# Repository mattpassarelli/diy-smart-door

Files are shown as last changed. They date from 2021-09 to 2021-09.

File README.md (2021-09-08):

# DIY Smart Door
This is, ideally, going to be a relatively universal smart door/lock adapter made from an ESP8266/ESP32 and one-two MG995 servos. More on what each servo does in the next section. This would then be connected to my home WiFi network where I can integrate it into Home Assistant for any kind of automation I would want to add, like opening the door for my friends without the need of me getting up from the couch :). 

## Design

Using an ESP8266 specifically (as I save my ESP32's for other projects), it's going to have 2 servos wired to it to open my door. If you choose the copy this project, I would guarantee you that like >90% of people only need 1 servo. ~~My current apartment's door is this weird style I've never seen where you *have* to use the key to open the door, regardless of whether or not anything is locked. Meaning, I only really have a deadbolt, and not a latch lock that I can engage and disengage. So even if I left the deadbolt unlocked all the time, you would need a key to be able to turn my door's latch and handle to enter my apartment.~~ I have what's called a Store Room style latch. I'm going to work off the assumption that my apartment will switch it out for me (going off the reasons that I risk getting locked out frequently, which technically isn't wrong); so we'll only need the one main servo for now*.

So, now the mechanical design ideas; There are a few 3D models in this repo that should be fairly universal. Right now, both planned and ready are:
- the housing for the servo that will be secured to the door over the deadbolt
- the latch cover that goes over my deadbolt and fits one of the servo horns
- a housing for the arduino and a battery and charger
- and the servo housing for the door handle portion*

That list might be updated as I add or remove parts from my design.

There are also 2-3 buttons for this system: 

- a lock button
- an unlock button
- an unlock iff locked, then turn handle button*

### Servo One
The first servo will be secured in housing that is then, most likely, command stripped to the door. 1) because I don't want to damage the door by screwing into it, and 2) if something were to happen where I need to immediately exit my home, I could rip the whole thing off in one swoop and then repaint easily if anything got damaged. 

This servo is connected to the deadbolt by an adapter that sits on top of the bolt and has a horn glued into it. The first motion of the whole overarching code will be to turn this servo 150° clockwise to unlock, then the same degrees counter clockwise to close (the number will change based on your deadbolt, so be sure to measure). This will have a timer running, so that if the lock is unlocked for, say 10 minutes, it will automatically lock it, giving me some peace of mind. I do also plan on integrating some automation logic into this with Home Assistant that might mitigate the need for this, but either will do the trick. 

Right now, this is controlled by a button on my breadboard, but I have plans to automate this with Home Assistant later.

### Servo Two, the door "opener"*
This is the one that not everyone will need, but you may need something like Servo One attached to your latch lock if you have a "normal" door. This one will be to the side of the deadbolt, positioned directly above the very edge of the door handle. With a stiff rod attached to a horn, maybe like a hanger wire or wooden dowel, and the other end on a free moving pivot on the door handle, this servo will turn *after* the deadbolt is unlocked and if **and only if** the deadbolt is fully unlocked. This is will the last part of my "hardware portion" of this project, so this might vary greatly by the time I've figured out how best to do this.

This one will be a third button that unlocks the deadbolt if it isn't already unlocked, then turn the servo, "opening" the door for someone to be able to push open the door. Then it will release the handle after a very short amount of time, say 5 seconds, so that the door can close on it's own and lock itself like normal (I have one of those hydraulic arms attached the top of the door that automatically closes it and was there when I signed my current apartment).

*Right now, I'm trying to get my door handle's replaced by the apartment (so they still have legal, master access when needed). So this second servo will ideally be unneeded (or possible replaced by one that turns the little latch on a typical "privacy" style door latch).*

## Power

Nothing too special here, but will probably need some tuning. I have a 3.7V 4400mAh battery laying around that I intend to use. I grabbed [this USB Type C charging circuit here from Adafruit](https://www.adafruit.com/product/4410) and will use that to charge the whole circuit. While power draw will vary wildly based on how often the locks are opened and closed, I expect this to last a solid amount of time between charges.

[This Adafruit forum page](https://forums.adafruit.com/viewtopic.php?f=8&t=61747#wrap), specifically the comments by `adafruit_support_mike` were super helpful in making a really simple battery wiring circuit for this. Basically just use the picture OP made, replacing the joint wires with the comments made by Mike. 

## Write Code

As a small side note, it turns out that PlatformIO handles the servo library differently (or wrong) so it caused my servos to turn really slowly and not go the full distance that I had coded. So instead of trying to debug it, I have an Arduino IDE .ino file of `main.cpp` so that I can use Arduino's IDE to write the code and have it work as intended.

## Home Assistant and Google Home Integrations

This is the really fun stuff here. Let's start with getting it integrated into HA, then we'll do Google.

### Home Assistant

Initially, I wanted to use ESPHome, a system built for Home Assistant that (from what I understand), writes the code for you to your ESP based boards, to do specific tasks. Unfortunately, Servos aren't officially support by HA and the workarounds they offer didn't seem like they'd offer enough versatility to do what I needed. So in the main code here, we setup a really *really* simple web server on the board, along with a static IP so it never changes. This web server takes simple GET requests from any client and then performs the respecitive command that the function calls. 

e.g

```
void openLockRemotely() {
    if (isUnlocked) {
        httpRestServer.send(500, "text/html", "Deadbolt is already unlocked");
    }
    openLock();
    httpRestServer.send(200, "text/html", "Deadbolt is now unlocked");
}

void restServerRouting() {
    httpRestServer.on("/", HTTP_GET, []() {
        httpRestServer.send(200, F("text/html"),
                            F("Welcome to the Smart Door!"));
    });
    httpRestServer.on(F("/openLock"), HTTP_GET, openLockRemotely);
    httpRestServer.on(F("/closeLock"), HTTP_GET, closeLockRemotely);
    httpRestServer.on(F("/getLockStatus"), HTTP_GET, getLockStatus);
}
```
The rest server is listening on the current 3 endpoints, `openLock closeLock & getLockStatus`. When you go to `http://<BOARD'S_IP_ADDRESS>:8080/openlock` it will call `openLockRemotely` which is just a wrapper function for `openLock` and then returns a really simple HTTP 200 code so we know that the function completed. 

`getLockStatus` returns the value of the boolen `isUnlocked` and then this is displayed in HA for us to see.

What I did to make these call-able from HA is to use the REST integration built into HA that is then called from different automations and scripts. In your `configuration.yaml` you'll want to add something like the following, changing the url and/or names to suite your case:

```
rest_command:
  open_door_lock:
    url: "http://192.168.0.177:8080/openLock"
    method: get
    content_type: "application/x-www-form-urlencoded"
  close_door_lock:
    url: "http://192.168.0.177:8080/closeLock"
    method: get
    content_type: "application/x-www-form-urlencoded"
```

We'll then call these rest commands from an automation, like the one used to unlock the deadbolt:
```
alias: Unlock Deadbolt
description: ''
trigger: []
condition: []
action:
  - service: rest_command.open_door_lock
mode: single
```
As a note: I greatly prefer doing automation and script making from the Home Assistant GUI, these YAML file examples are mostly just for reference, but you could copy and paste them into the YAML editors instead.

I also use a script to call the REST command, which is used in some of the Apple Watch complications I wanted to use:
```
sequence:
  - service: rest_command.open_door_lock
mode: single
alias: Unlock Front Door
icon: mdi:lock-outline
```

From here, you can setup the LoveLace UI however you'd prefer to in order to make use of these automations. If you'd like to copy what I use, this is the YAML code for it:
```
type: vertical-stack
cards:
  - type: glance
    entities:
      - entity: sensor.deadbolt_status
    title: Front Door
    show_icon: true
    state_color: false
  - type: horizontal-stack
    cards:
      - entity: automation.lock_deadbolt
        tap_action:
          action: call-service
          service: rest_command.close_door_lock
          service_data: {}
          target: {}
        type: button
        icon: mdi:lock-outline
        icon_height: 48px
        hold_action:
          action: none
      - type: button
        tap_action:
          action: call-service
          service: rest_command.open_door_lock
          service_data: {}
          target: {}
        entity: automation.unlock_deadbolt
        icon_height: 48px
        hold_action:
          action: none
        icon: mdi:lock-open-outline
```

And it looks like this [![UI Exmaple]](https://imgur.com/rwhDQag)

### Google Assistant Integrations

First step here is to integrate Google with HA. There are a few ways to do this, and you can find documentation on it on the HA docs website, as it's too much to cover in a README here. I actually wound up subscribing to Home Assistant Cloud as it's only $5/month and the intregation with Google (and Alexa) is essentially one click. 

Once you have Google integrated, you'll want to expose the scripts to Google from HA. You can do this from `Configuration >> Home Assistant Cloud >> Google Assistant` and then select manage entities. Make sure that the two scripts we made for Locking and Unlocking the deadbolt are checked off. On a side note, I'd recommend un-exposing anything that's already integrated into GA, as it caused duplicates for everything I already had set up, which was annoying to resolve before learning of this.  

With the scripts and other entities exposed, bo back and click the `Sync Entities To Google` button and then open Google Assistant/Google Home on your phone or tablet (or chomebook maybe?) and tell it to "Sync my devices." From here, any entities you synced will become visible in the "Unassigned" Room, but not scripts! Scripts are usable, but since they aren't entities, they aren't assigned an object or room in Google Home. You can still say "Hey/Okay Google, *run* <SCRIPT_NAME>" and it'll execute. 

If, like me you'd prefer a more natural language way of doing this, set up a routine in Google Home. So, for example I set one up that activates on the phrase "Unlock the front Door" and this triggers the script, which you can set from `Add Action >> Adjust Home Devices >> Adjust Scenes >> <YOUR_SCRIPT_NAME>`.

However you set it up, rountine or not, this will trigger the Home Assistant Script we wrote, which triggers the REST Command, which calls the arduino that then activates the corresponding function to lock or unlock the deadbolt. Sounds convoluted, but this chain is probably how most commerical smart door locks operate, give or take the HA integrations.

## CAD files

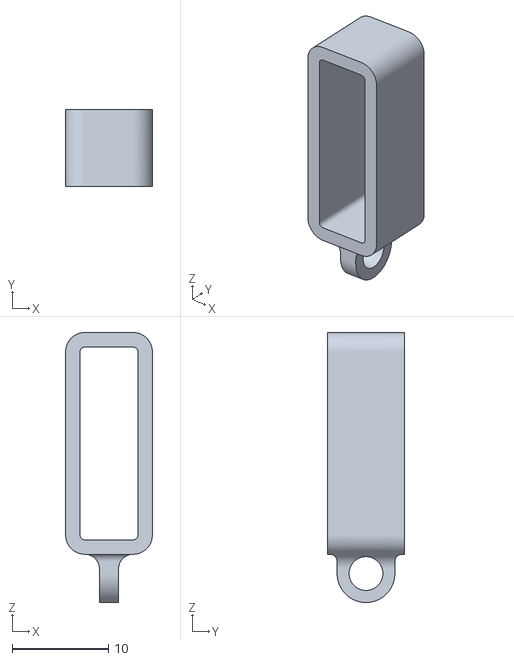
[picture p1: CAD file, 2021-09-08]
3D Prints/Door Handle Grip.stl
9.00 x 8.00 x 28.0

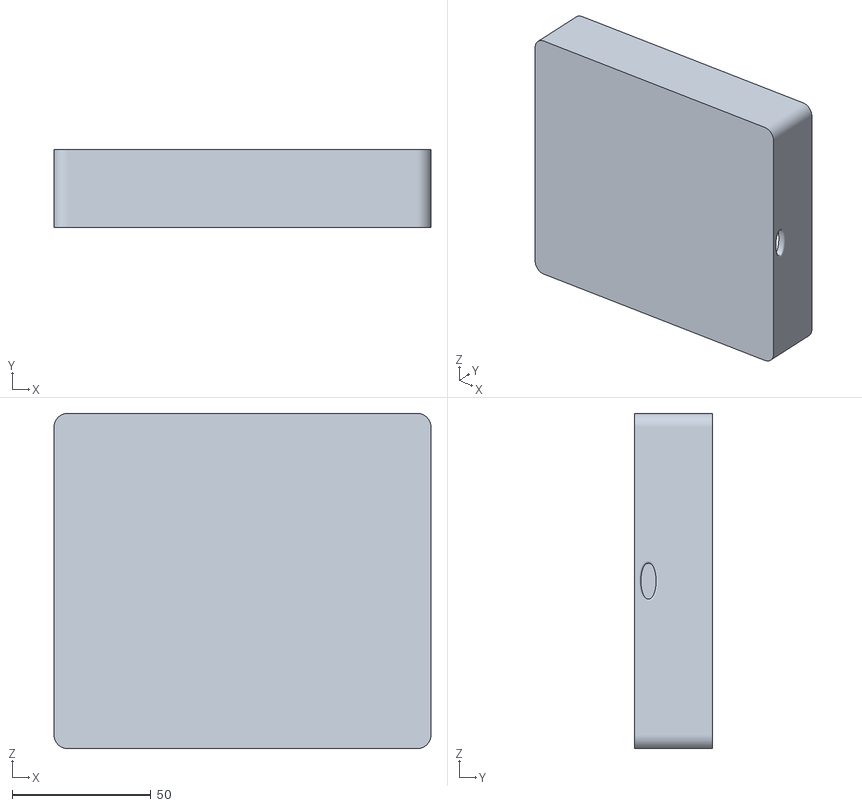
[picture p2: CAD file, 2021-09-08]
3D Prints/Box.stl
136.0 x 28.0 x 121.0

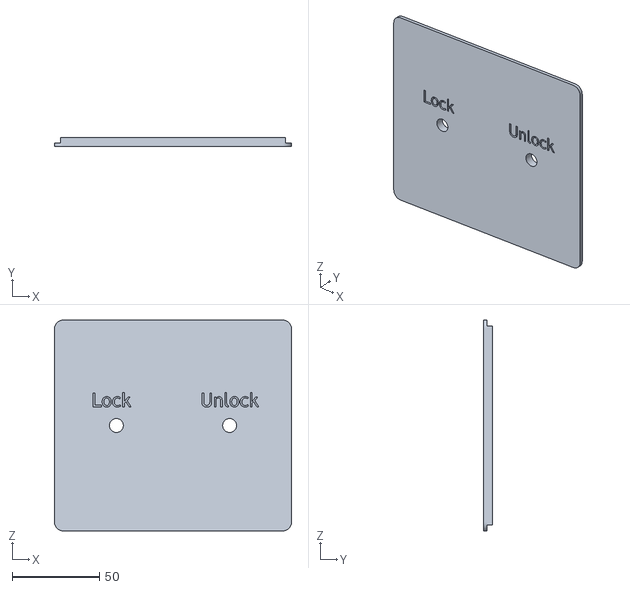
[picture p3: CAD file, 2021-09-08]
3D Prints/2 Hole Lid.stl
136.0 x 5.00 x 121.0

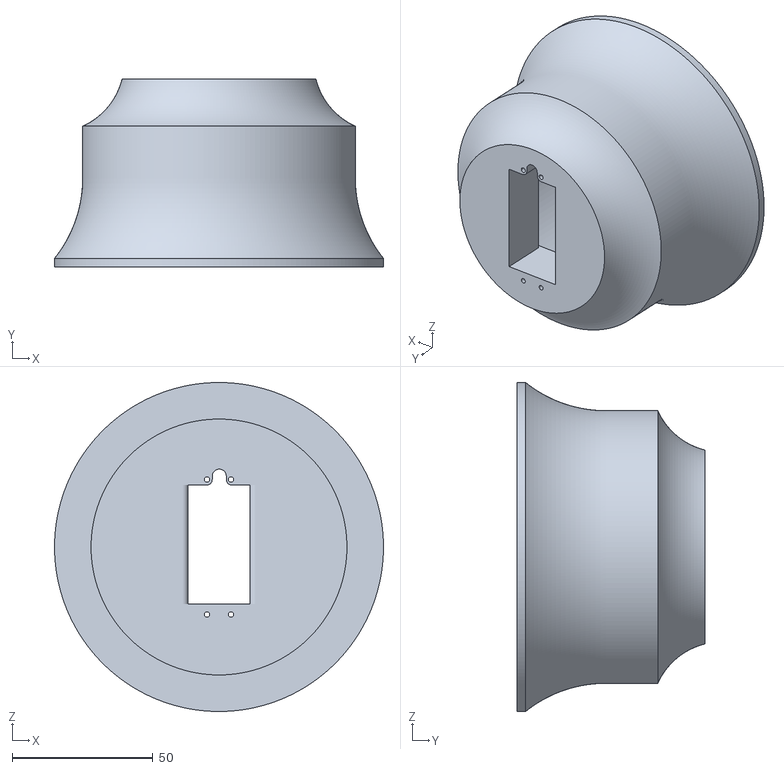
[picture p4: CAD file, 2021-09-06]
3D Prints/Door Mount.stl
117.0 x 66.7 x 117.0

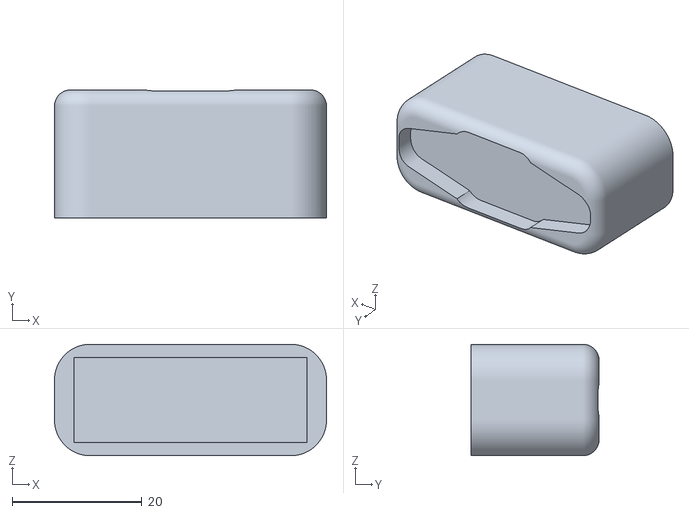
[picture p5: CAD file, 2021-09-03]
3D Prints/Bolt Cover.stl
42.0 x 19.8 x 17.2

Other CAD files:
3D Prints/Lid.stl

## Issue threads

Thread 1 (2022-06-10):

battery life

lclem, 2022-06-10:
hello, how long does the battery last when the system is idle?
i.e., are we talking about on the order of 1 day, 1 week, or 1 month?

mattpassarelli, 2022-06-10:
I moved at the start of the year and haven't used it since, so it's been a while. But nothing some simple math can't tell us! You can estimate how long something will last off battery power by doing (capacity of the battery in mAh)/(the power draw of your device in mA). Obviously power draw will vary based on different factors like if you use a different board or how often the servo spins.

But for this specific board and now including any servos, we can do 4400mAH (the size of battery I used)/~50mA (based on this power draw chart here https://bbs.espressif.com/viewtopic.php?t=133). Since the code I wrote has the device constantly looking to a REST server for commands, it never really gets a chance to enter sleep; a good place for optimization. But that exact configuration should give you about ~88 hours of constant on time, give or take the factors mentioned above.

Closed 2022-06-10.

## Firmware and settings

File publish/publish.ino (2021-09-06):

#include <Arduino.h>
#include <EEPROM.h>
#include <ESP8266WebServer.h>
#include <ESP8266WiFi.h>
#include <Servo.h>

#include "secrets.h"

#define WIFI_SSID _WIFI_SSID  //found in secrets.h (ignored by git)
#define WIFI_PASSWORD _WIFI_PASSWORD
#define HTTP_REST_PORT 8080

ESP8266WebServer httpRestServer(HTTP_REST_PORT);
IPAddress ip(192, 168, 0, 177);
IPAddress dns(192, 168, 0, 1);
IPAddress gateway(192, 168, 0, 1);
IPAddress subnet(255, 255, 255, 0);

int servoPin = 2;
int tryCount = 0;
int openButton = 10;
int closeButton = 9;
bool isUnlocked;
Servo Servo1;

void openLock() {
    if (isUnlocked) {
        return;
    }

    int pos;
    Servo1.attach(servoPin);
    for (pos = 0; pos <= 155; pos += 1) {
        Servo1.write(pos);  // tell servo to go to position in variable 'pos'
        delay(15);          // waits 15ms for the servo to reach the position
    }
    Servo1.detach();
    isUnlocked = true;
}

void closeLock() {
    if (!isUnlocked) {
        return;
    }

    int pos;
    Servo1.attach(servoPin);

    for (pos = 155; pos >= 0; pos -= 1) {
        Servo1.write(pos);  // tell servo to go to position in variable 'pos'
        delay(15);          // waits 15ms for the servo to reach the position
    }
    Servo1.detach();

    isUnlocked = false;
}

void openLockRemotely() {
    if (isUnlocked) {
        httpRestServer.send(500, "text/html", "Deadbolt is already unlocked");
    }
    openLock();
    httpRestServer.send(200, "text/html", "Deadbolt is now unlocked");
}

void closeLockRemotely() {
    if (!isUnlocked) {
        httpRestServer.send(500, "text/html", "Deadbolt is already locked");
    }
    closeLock();
    httpRestServer.send(200, "text/html", "Deadbolt is now locked");
}

//return isUnlocked so I can see the status in HA
void getLockStatus() {
    const String status = isUnlocked ? "no" : "yes";

    httpRestServer.send(200, "text/html", "Deadbolt is locked: " + status);
}

/**
 * Ideally, I wanted to hook the ESP directly into HA
 * But I can't find a proper way to do that. ESPHome exists
 * but it doesn't seem to do what I want, so I setup a webserver
 * to handle simple REST calls to open and close the locks
 * */
void restServerRouting() {
    httpRestServer.on("/", HTTP_GET, []() {
        httpRestServer.send(200, F("text/html"),
                            F("Welcome to the Smart Door!"));
    });
    httpRestServer.on(F("/openLock"), HTTP_GET, openLockRemotely);
    httpRestServer.on(F("/closeLock"), HTTP_GET, closeLockRemotely);
    httpRestServer.on(F("/getLockStatus"), HTTP_GET, getLockStatus);
}

void setup() {
    // put your setup code here, to run once:
    Serial.begin(115200);

    Servo1.attach(servoPin);
    Servo1.write(90);
    Servo1.detach();
    pinMode(openButton, INPUT_PULLUP);
    pinMode(closeButton, INPUT_PULLUP);

    WiFi.config(ip, dns, gateway, subnet);
    WiFi.begin(WIFI_SSID, WIFI_PASSWORD);
    Serial.print("Beginning WiFi Connection to: ");
    Serial.println(WIFI_SSID);

    int i = 0;
    while (WiFi.status() != WL_CONNECTED) {  // Wait for the Wi-Fi to connect
        delay(1000);
        Serial.print(++i);
        Serial.println(' ');
    }

    Serial.println('\n');
    Serial.println("Connection established!");
    Serial.print("IP address:\t");
    Serial.println(WiFi.localIP());
    WiFi.setAutoReconnect(true);

    //start http server stuff
    restServerRouting();
    httpRestServer.begin();
}

void loop() {
    //Button Detections
    if (digitalRead(openButton) == LOW) {
        Serial.println("openButton Pressed");
        openLock();
    } else if (digitalRead(closeButton) == LOW) {
        Serial.println("closeButton Pressed");
        closeLock();
    }

    //WiFi Disconnect detection
    if (WiFi.status() != WL_CONNECTED) {
        if (!isUnlocked) {
            Serial.println("WARNING: WiFi signal was lost!! Unlocking deadbolt for safety");
            //TODO: Add transistor switch
            openLock();
        }
    }

    //http server stuff
    httpRestServer.handleClient();
}

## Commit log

2021-09-03 Initial Commit. Simple servo turning code and structure
    [Bolt Cover.stl]
2021-09-06 restarted project structure for PIO. added server code to hand REST calls for deadbolt servo
    [Door Mount.stl]
2021-09-06 fixed issues with servo turning distance. added a finalized imo file. see readme
    [publish.ino]
2021-09-08 added components box with 2 lid styles. Updated README
    [2 Hole Lid.stl, Box.stl, Door Handle Grip.stl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]
